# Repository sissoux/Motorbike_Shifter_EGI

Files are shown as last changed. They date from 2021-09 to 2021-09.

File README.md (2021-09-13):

# Motorbike_Shifter_EGI
Motorbike Shifter and engaged gear indicator

This project intend to complete this tutorial http://www.jbx9.16mb.com/index.php?page=GIND and achieve motorcycle engaged gear indicator + Shift light by measuring actual engine speed and engaged gear.

RPM is aquired through the Alternator. Votlage between two phases is picked up and shaped by "RPM Signal Conditioning" stage. Then it's isolated by an optocoupler and fed into the Micro controler.

Mechanical modification on the shifter allows to short one wire to bike ground when corresponding gear is engaged. Each wire is connected to a different voltage divider "step". Result is 6 discrete voltage steps barely equally distributed between 0 and 5V. Correspondance table is given in schematic.

An ATTiny84 MCU does the signal analysis and drives 6 independant outputs which can be connected on embeded LEDs or externalized using header connector.

PCB files are available at https://circuitmaker.com/Projects/Details/Alexis-Damiens-2/Shift-light

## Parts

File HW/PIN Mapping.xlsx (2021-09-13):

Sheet: PIN Mapping
PIN N° | Port | Net Name | Direction | Default state | Special feature
13 | PA0 | Gear_Input | INPUT | HiZ | ADC
12 | PA1 | D1 | OUTPUT | LOW | NA
11 | PA2 | D2 | OUTPUT | LOW | NA
10 | PA3 | D3 | OUTPUT | LOW | NA
9 | PA4 | D4_SCK | OUTPUT | LOW | NA
8 | PA5 | D5_MISO | OUTPUT | LOW | NA
7 | PA6 | D6_MOSI | OUTPUT | LOW | NA
6 | PA7 | RPM_IN | INPUT | HIZ | INPUT COMPARE
 | DDRA | 7E
2 | PB0 | NC
3 | PB1 | NC
5 | PB2 | NC
4 | PB3 | RESET

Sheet: ADC Values
ADC Resolution | 10
ADC Reference | 5 |  |  |  | REFS1 | REFS0 | MUX5 | MUX4 | MUX3 | MUX2 | MUX1 | MUX0 | HEX | Comment
Vresolution | 0.00488 |  |  | ADMUX | 0 | 0 | 0 | 0 | 0 | 0 | 0 | 0 | 0 | Vcc used as reference, ADC0 Selected
 |  |  |  |  | ADEN | ADSC | ADATE | ADIF | ADIE | ADPS2 | ADPS1 | ADPS0
 |  |  |  | ADCSRA | 1 | 0 | 0 | 0 | 0 | 0 | 1 | 0 | 82 | Enable ADC
1 | 0 | 0 | 82
2 | 0.8 | 164 | 256
3 | 1.7 | 348 | 430
4 | 2.5 | 512 | 594
5 | 3.3 | 676 | 758
6 | 4.1 | 840 | 932
0 | 5 | 1024

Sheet: Input Capture
 | COM1A1 | COM1A0 | COM1B1 | COM1B0 |  |  | WGM11 | WGM10
TCCR1A | 0 | 0 | 0 | 0 | 0 | 0 | 0 | 0
 | ICNC1 | ICES1 |  | WGM13 | WGM12 | CS12 | CS11 | CS10
TCCR1B | 1 | 0 | 0 | 0 | 0 | 0 | 1 | 1
 | FOC1A | FOC1B
TCCR1C | 0 | 0 | 0 | 0 | 0 | 0 | 0 | 0
 |  |  | ICIE1 |  |  | OCIE1B | OCIE1A | TOIE1
TIMSK1 | 0 | 0 | 1 | 0 | 0 | 0 | 0 | 0

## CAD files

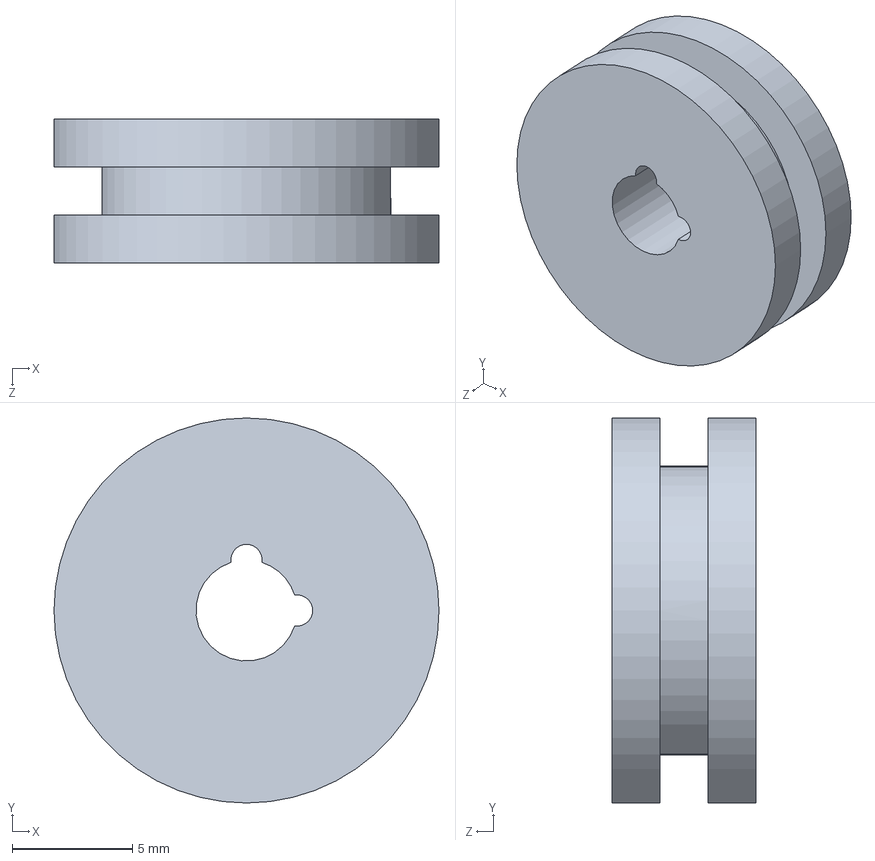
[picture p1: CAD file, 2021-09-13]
HW/passe cable.SLDPRT
16.0 x 16.0 x 6.00 mm

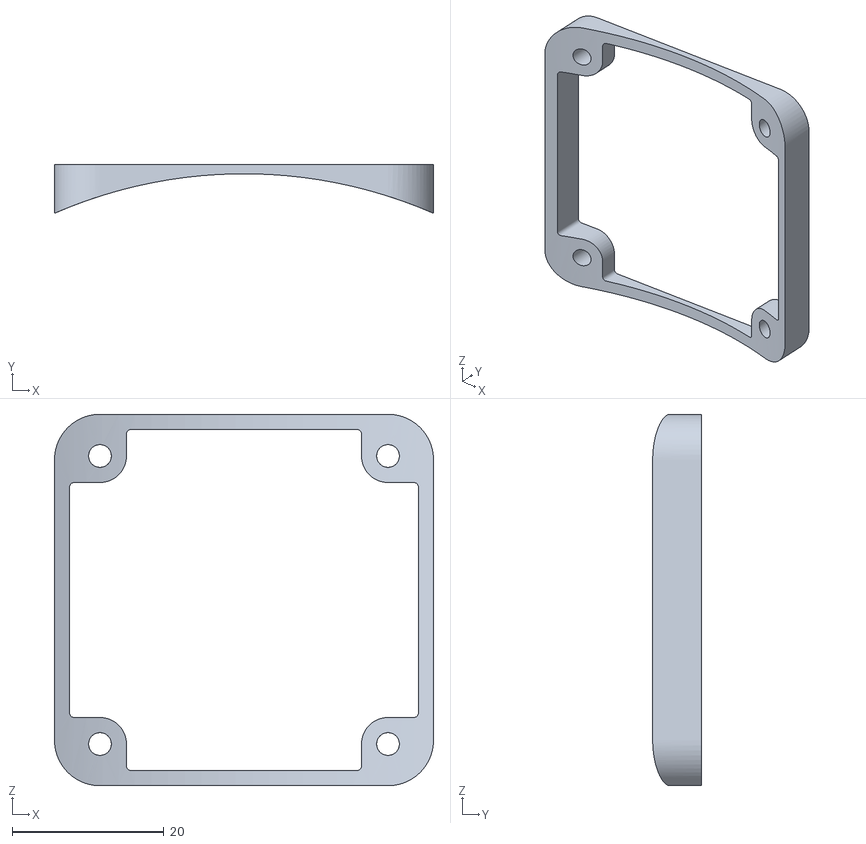
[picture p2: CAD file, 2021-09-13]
HW/Shifter Housing hole fixture.STL
50.0 x 6.42 x 49.0

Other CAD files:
HW/Shifter Housing.SLDPRT
HW/Shifter Housing.STL
HW/passe cable.STL

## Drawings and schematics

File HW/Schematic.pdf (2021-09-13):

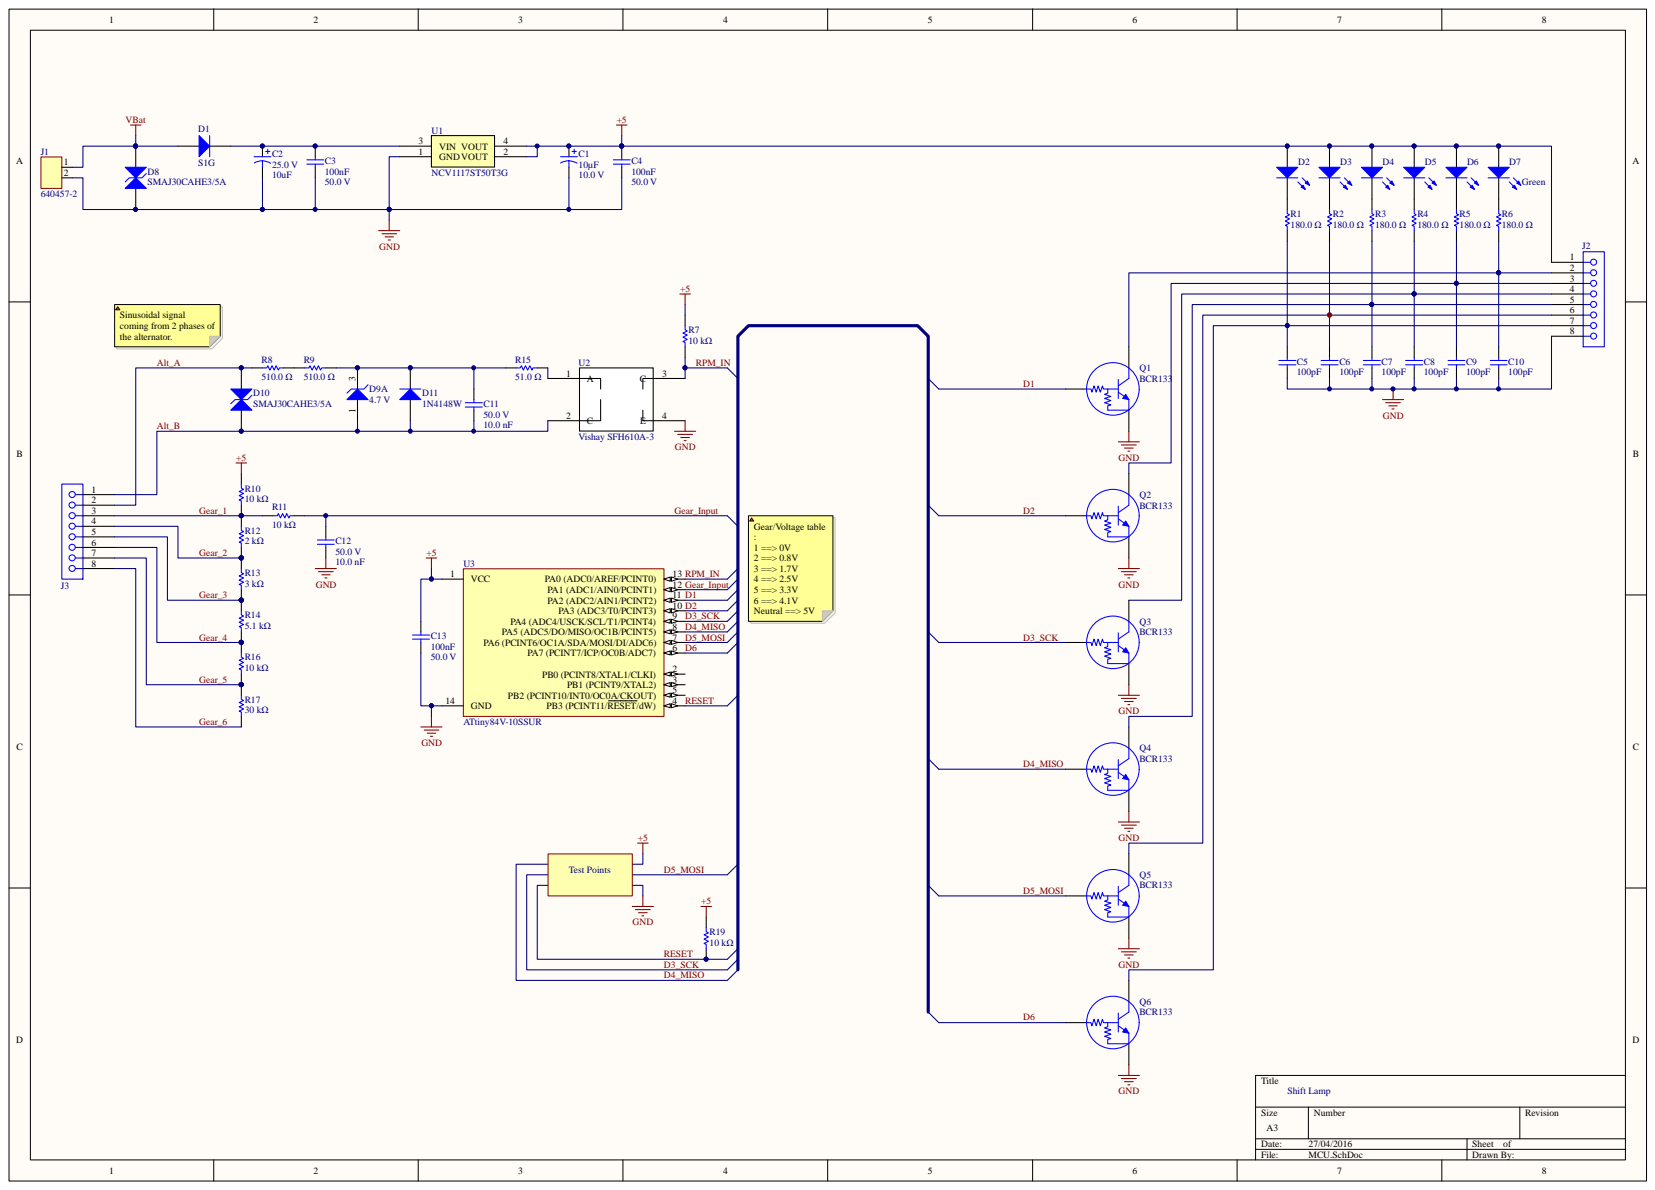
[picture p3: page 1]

Sinusoidal signal
coming from 2 phases of
the alternator.

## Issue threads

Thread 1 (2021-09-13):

Gear state is oscillating when engine is started

sissoux, 2021-09-13:
During usage when gear is started, voltage variation are occuring on gear sense line ==> Add SW filtering.

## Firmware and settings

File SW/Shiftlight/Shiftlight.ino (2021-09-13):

#define GEAR_IN_PIN PIN_PA0
#define D1_PIN PIN_PA1
#define D2_PIN PIN_PA2
#define D3_PIN PIN_PA3
#define D4_PIN PIN_PA4
#define D5_PIN PIN_PA5
#define D6_PIN PIN_PA6
#define RPM_IN_PIN PIN_PA7
// 0 0.8 1.7 2.5 3.3 4.1

uint16_t GearDetectionTable[6] = {930, 757, 593, 429, 255, 81};


void setup() {
  // put your setup code here, to run once:
  pinMode(GEAR_IN_PIN, INPUT);
  pinMode(RPM_IN_PIN, INPUT);
  pinMode(D1_PIN, OUTPUT);
  pinMode(D2_PIN, OUTPUT);
  pinMode(D3_PIN, OUTPUT);
  pinMode(D4_PIN, OUTPUT);
  pinMode(D5_PIN, OUTPUT);
  pinMode(D6_PIN, OUTPUT);
  for (int i = 0; i < 2; i++)
  {
    for (int index = 1; index < 7; index++)
    {
      PORTA = (0x80 >> index) & 0x7e;
      delay(50);
    }
    for (int index = 1; index < 7; index++)
    {
      PORTA = (0x01 << index) & 0x7e;
      delay(50);
    }
  }
}

void loop()
{
  uint8_t currentgear = getGear(analogRead(GEAR_IN_PIN));
  if ( currentgear >= 0 && currentgear <= 6)
  {
    PORTA = (0x80 >> getGear(analogRead(GEAR_IN_PIN))) & 0x7e;
  }
  else PORTA = 0;
  delay(10);
}

uint8_t getGear(uint16_t analogValue)
{
  if (analogValue > GearDetectionTable[0]) return 0;

  for (int i = 1; i < 6; i++)
  {
    if ( analogValue > GearDetectionTable[i]) return 7 - i;
  }
  return 1;
}
